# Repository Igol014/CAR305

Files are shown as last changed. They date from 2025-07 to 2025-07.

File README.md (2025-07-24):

# Инструкция по сборке и запуску автономной модели автомобиля RC305

## Вам понадобится следующий набор инструментов
  - Паяльник (думаю понятно для чего 🤔)
  - Шуруповерт (для рассверливания крепежных отверстий и сверления новых 👍)
  - Клеевой пистолет (для укладки проводов в корпусе, фиксации разъема аккумулятора, да и просто на случай, если увлеклись сверлением 🙊)
  - Отвертки (скорее всего PH1 и PH2, но зависит от использованных винтиков 🤷‍♂️)
  - Шестигранники (если не хватит обычных винтиков 😎)
## Использованные компоненты
  - Колесо диаметром 88 мм 4 шт;
  - Мини-компьютер Raspberry Pi 5 8 GB Cortex-A76;
  - Понижающий DC-DC 5A XL4005 2 шт;
  - Мотор-редуктор с энкодерами 2 шт;
  - Драйвер L298N;
  - Тумблер-выключатель;
  - Arduino Nano V3.0 USB-C ATMEGA328P FT232(Old Bootloader);
  - Набор проводов для пайки;
  - Аккумулятор LiPo 4S 3300 mAh 40C(NXE) 14.8В;
  - Лазерный дальномер(LiDAR) для робота-пылесоса Xiaomi Mijia Mi Robot Vacuum Cleaner 1S;
  - Модуль IMU 9-DOF GY-85;
  - Сервопривод TianKongRC TD-8120MG;
  - Пины мама-мама 20 шт.
## Корпус

Модель корпуса нашей машинки выглядит следующим образом

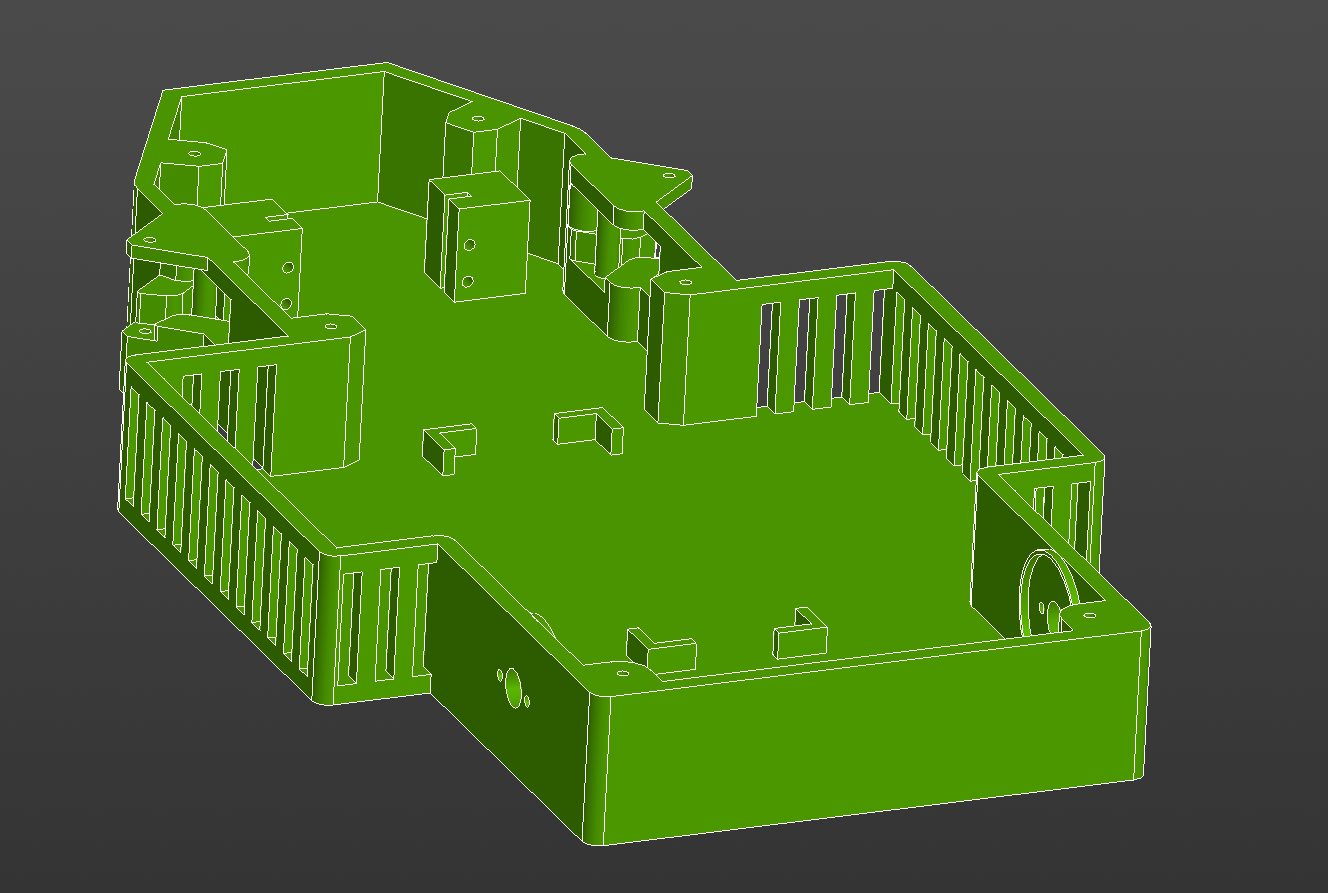
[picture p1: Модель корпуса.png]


Если нет собственных "производственных мощностей", всегда можно воспользоваться услугами __[студий 3D печати](https://uslugi.yandex.ru/213-moscow/category/raznoe/poligraficheskie-uslugi/3dpechat--5635)__

В случае выбора лёгкого пути, смело можно пропускать данный раздел

Для печати корпуса необходим 3D принтер с рабочим полем **400x300 мм**

Выбор материала

Краткая информация об основных видах пластика

| **Параметр** | **ABS** | **PLA** | **PETG** |
|---|---|---|---|
| **Печать** | Капризен, требует закрытого бокса и вентиляции | Очень прост, идеален для новичков | Умеренно прост, требует настройки |
| **Прочность** | Прочный, ударостойкий | Жесткий, но хрупкий при ударе и холоде | Прочный, гибкий, устойчив к излому |
| **Темп. стойкость** | Высокая (-40…+80 °C) | Низкая (~50 °C, "плывёт" на солнце) | Средняя (~80 °C), подходит для большинства задач  |
| **Нетоксичность** | ❌ (выделяет вредные пары) | ✅ (безопасен, с запахом жареной еды) | ✅ (не пахнет, безопасен) |

Для нашего автомобиля будем использовать **PETG**

Для печати корпуса воспользуемся специальной программой __[OrcaSlicer](https://orcaslicer.com/)__

Выставим основные параметры печати следующими:

- Температура экструзии — 215-245°C;

- Температура стола — 20-80°C;

- Процент заполнения — 60%;

## Устанока навесных компонентов
Во время установки ориентируйтесь на компоновку деталей с фотографии ниже.

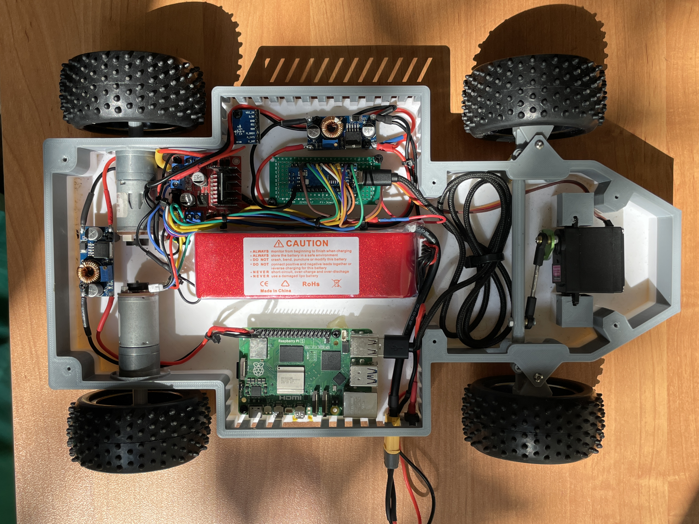
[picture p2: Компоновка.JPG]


1) Начнём с установки двигателей и задних колёс;
    - Закрепите задние моторы на корпус винтами M3;
    - Установите втулки на валы моторов и зафиксируйте их сбоку винтом чрез специальное отверствие во втулке винтом M3;
    - Установите колесо на втулку, зафиксируйте колесо на валу винтом M4.
2) Монтаж передних колес и рулевого управления;
    - Установите поворотные кулаки на винты M3;
    - Установите сервопривод, закрепите его винтами M2.5;
    - Соедините тягу сервопривода к переходной пластине сервопривода;
    - Соедините поворотные кулаки рулевой рейкой с помощью винтов M3;
    - Соедините рулевую рейку с тягой сервопривода.
    - Установите гайку-проставку на колесо и вставьте в поворотный кулак. Закрепите колеса винтами M4, затянув с небольшим усилием с внутренней стороны колеса самоконтрящуюся гайку.
3) Далее монтируем стойки для установки __Raspberry Pi 5__, __лидара__, __2-ух DC-DC преобразователей__, __IMU__ и __Arduino Nano__. Стойки для лидара устанавливаем на крышку корпуса, делаем отверстие в крышке для вывода проводов. Устанавливать лидар можно в произвольном месте(__Для всех компонентов, помимо лидара, используйте низкие стойки, примерно 0.5 см высотой__);
4) Монтируем драйвер моторов, DC-DC преобразователи, IMU, сервопривод рулевого управления;
5) Устанавливаем кнопку питания в корпус, прокладываем провод питания с разъемом XT60 в корпусе;
6) Настраиваем преобразователи на **5В** путем вращения винта против часовой стрелки;
7) Монтируем Arduino;
8) Монтируем проводку по схеме(за исключением Raspberry Pi);

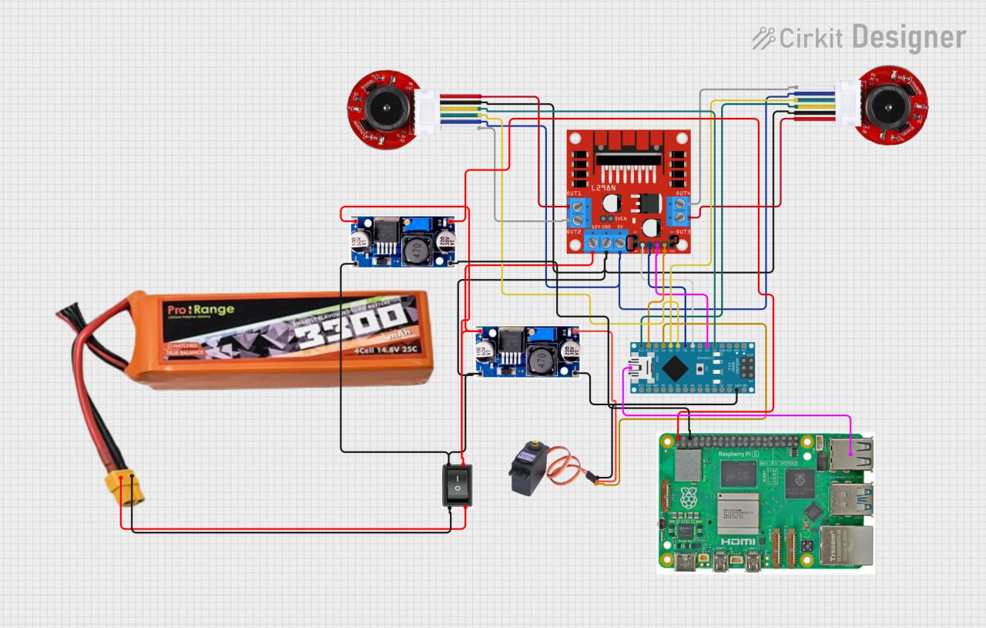
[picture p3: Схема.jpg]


9) Устанавливаем Raspberry Pi и подключаем ее согласно схеме;
10) Загружаем скетч на Arduino(__Обязательно к прочтению пункт с возможными проблемами перед работой с Arduino__);
11) Подключаем Arduino к Raspberry Pi через провод USB-C (__нужно использовать мягкий, гибкий провод, другой не подойдет__);
12) Крепим крышку(можно на винты, можно на саморезы)
13) Устанавливаете ОС Ubuntu на Raspberry Pi;
14) Подготовка Raspberry Pi к работе
      
    Для удаленного управления машинкой через Raspberry Pi был использован протокол SSH, с помощью которого можно получить доступ к терминалу и отправлять команды на малинку. Перед подключением по этому протоколу, нужно         сначала установить необходимые пакеты на Raspberry и провести некоторые манипуляции. Перед всеми махинациями нужно обновить системные пакеты во избежание различного рода ошибок во время установки. Сделать это можно следующей командой:

      ```
      sudo apt update
      ```
    - Установка SSH-сервера;
       
       Для установки SSH-сервера используем команду:
       ```
       sudo apt install openssh-server
       ```
    - Проверка статуса службы;
       
       Проводим проверку и убеждаемся в том, что установка прошла правильно и все работает штатно:
       ```
       sudo systemctl status ssh
       ```
    - Настройка фаервола(Если не планируете использовать - можно пропустить);
       
       Если вы хотите использовать фаервол, то в его настройках нужно разрешить подключеие к системе по протоколу SSH:
       ```
       sudo ufw allow ssh
       ```
       Если вы установили свой порт для подключения к серверу по протоколу SSH, то выполните следующую команду:(по умолчанию стоит порт 22, менять его не рекомендую):
       ```
       sudo ufw allow 'ваш порт'
       ```
       После выполнения вышеперечисленных команд, включаем фаервол:
       ```
       sudo ufw enable
       ```
    - Определить IP-адрес для подключения;
       
       Для определения IP-адреса нужно выполнить следующую команду:
       ```
       ip address
       ```
       После выполнения данной команды в терминале появится информация о различных сетевых интерфейсах. Нам нужно найти строку wlan и ниже нее будет нужная нам информация. Ищем строку, похожую на эту:
       ```
       inet 198.168.1.100/24
       ```
       В данном случае, IP-адрес - 198.168.1.100.
    - Подключение к Raspberry Pi по протоколу SSH через внешнее устройство;
       
       Для работы с SSH я рекомендую использовать программу [Termius](https://www.termius.com/). Она бесплатная, с приятным и понятным интерфейсом и большим количеством предоставляемых ползователю возможностей. Скачать ее можно в магазине приложений Microsft Store.
       После установки приложения ищем в интерфейсе кнопку NEW HOST. Справа появляется выпадающее меню. В колонке Address вводим IP-адрес, ранее нами полученный. После ищем колонку с названием 'SSH on 22 port'(22 меняем на свой порт, если во время установки порт по умолчанию был вами изменен). В этой колонке будут поля 'Username' и 'Password'. В них нужно ввести имя пользователя и пароль, которые вы задали во время установки Ubuntu на Raspberry Pi. Все, поздравляю, на этом настройка подключения закончена, ищем в этом выпадающем меню зеленую кнопку 'Connect' и можно работать удаленно с малинкой. Termius также поддерживает удаленную передачу файлов через SFTP, поэтому малинку можно смело ставить в корпус машинки и больше ее не трогать, все необходимые операции легко можно провести удаленно, без физического подключения к Raspberry Pi.
    - __Финал!__ Загружаем код на малинку и запускаем его.
   
       Termius, как я ранее уже писал, поддерживает работу с файлами. Для того, чтобы перенести наш [код](https://github.com/Igol014/RC305/blob/main/Код/rasp.py) на малинку, в приложении ищем сверху вкладку SFTP и подключаемся к Raspberry Pi. Предыдущее подключение должно сохраниться, поэтому тут ничего сложного, вам нужно нажать только одну кнопку.
       После подключения перед вами будет два поля: слева и справа. Слева - директории вашего компьютера, справа - директории малинки. Переносите его в удобную вам директорию.
        Далее, на Raspberry Pi нужно установить ПО для работы с Python:
       ```
       sudo apt install python3
       ```
       ```
       sudo python3 -m venv <RC305>
       ```
       ```
       source <RC305>/bin/activate
       ```
       ```
       pip install pyserial
       ```
       Для запуска нашей программы, переходим в директорию, в которую ранее разместили rasp.py с помощью команды:
       ```
       cd 'путь до нужной директории'
       ```
       После, вводим следующую команду:
       ```
       sudo python3 rasp.py
       ```
      
### Готово!



## Возможные проблемы

- Не увлекайтесь рассверливанием отверстий при установке рулевого управления и стоек для компонентов! В первом случае будет большой люфт рулевого управления, вследствие чего автомобиль не сможет ровно держать курс, а во втором случае стойки не будут надежно зафиксированы в корпусе, что в будущем приведем к произвольному демонтажу компонентов при эксплуатации.
- Холодная пайка - ваш враг. Хорошенько прогревайте контакты во время пайки, так как это исключит неприятные моменты, связанные с отошедшей пайкой или плохим контактом.
- Надежно фиксируйте провода в зажимах, в противном случае будет плохой контакт или вовсе его отсутствие.
- При работе с Arduino не подключайте ее напрямую к компьютеру, используйте USB-hub с внешним питанием. Не думаю, что вы будете использовать оригинальную Arduino, а китайские иногда сходят с ума, умирают сами и забирают за собой технику, подключенную к ней.
- Raspberry Pi подключаете к Arduino в самую последнюю очередь, когда проверили все контакты и соединения и убедились, что все работает в штатном режиме. Спалить малинку - очень неприятно.

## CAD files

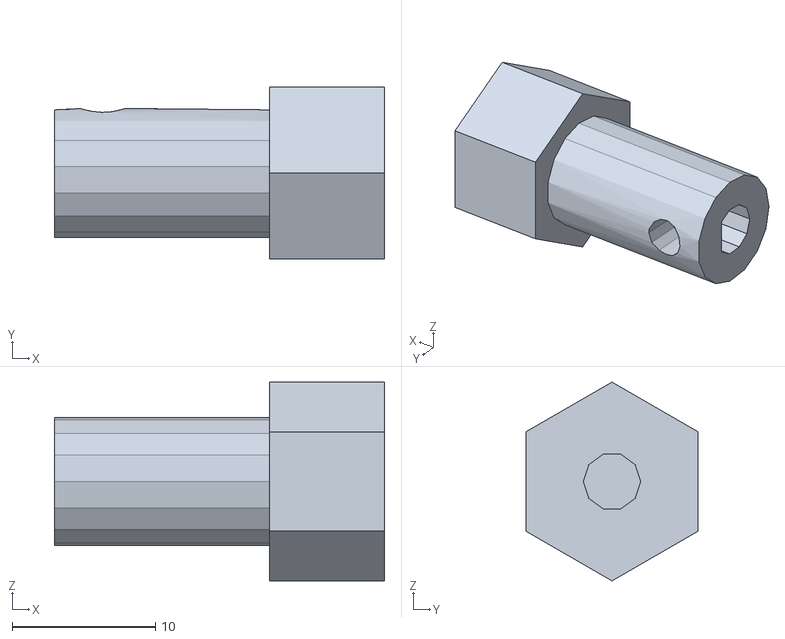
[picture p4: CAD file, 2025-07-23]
Модель/Втулка заднего колеса.stl
23.0 x 12.0 x 13.9

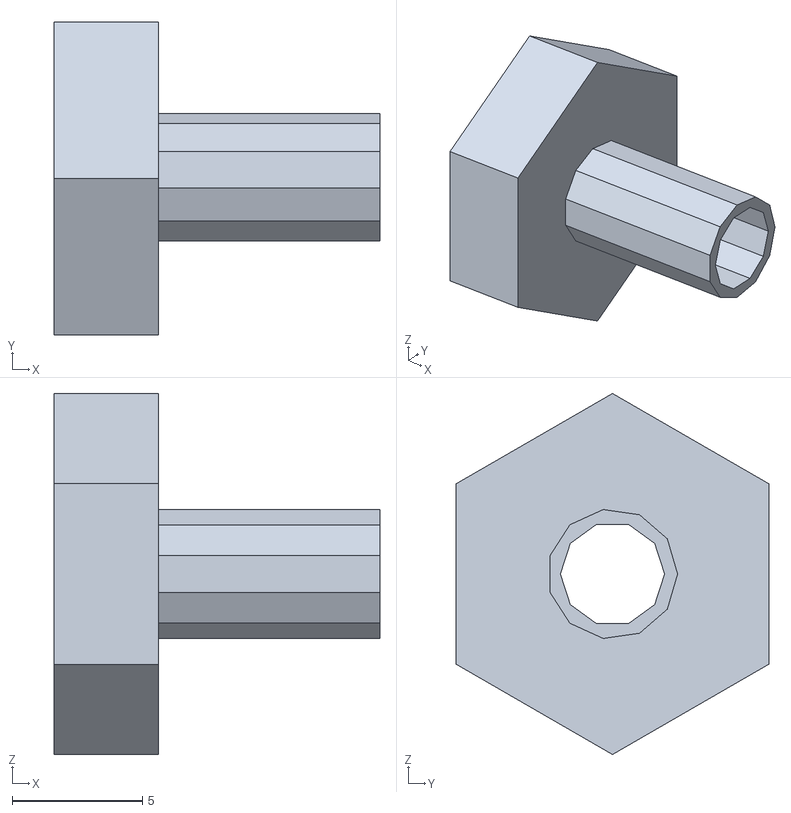
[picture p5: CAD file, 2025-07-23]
Модель/Гайка-проставка для колеса.stl
12.5 x 12.0 x 13.9

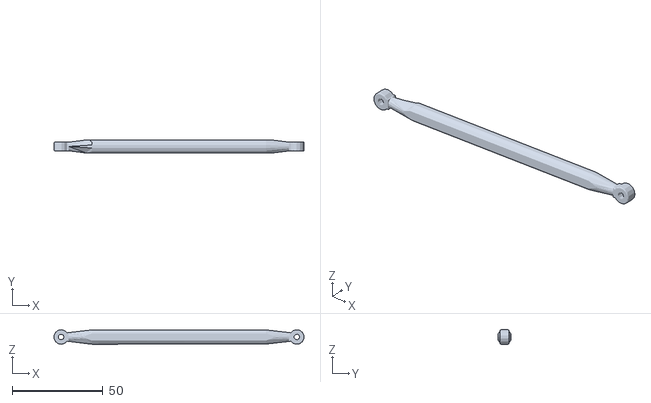
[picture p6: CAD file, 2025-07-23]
Модель/Рулевая тяга.stl
137.4 x 7.05 x 8.00

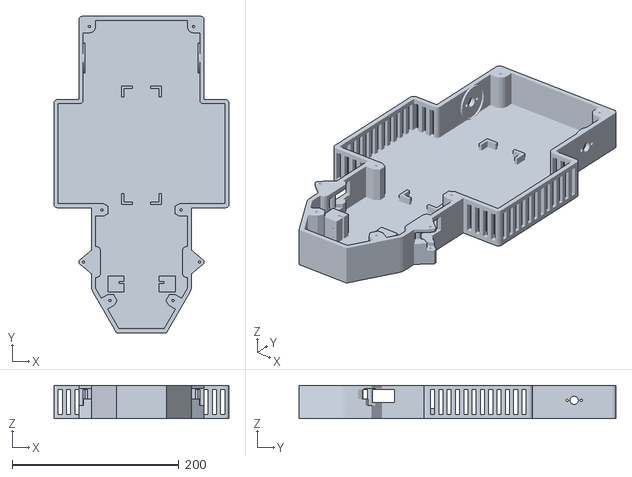
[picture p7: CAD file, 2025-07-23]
Модель/Рама.stl
210.0 x 380.0 x 40.0

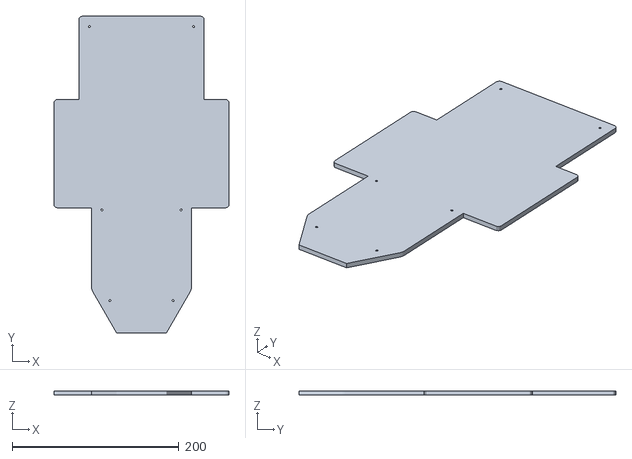
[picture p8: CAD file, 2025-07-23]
Модель/Крышка корпуса.stl
210.0 x 380.0 x 5.00

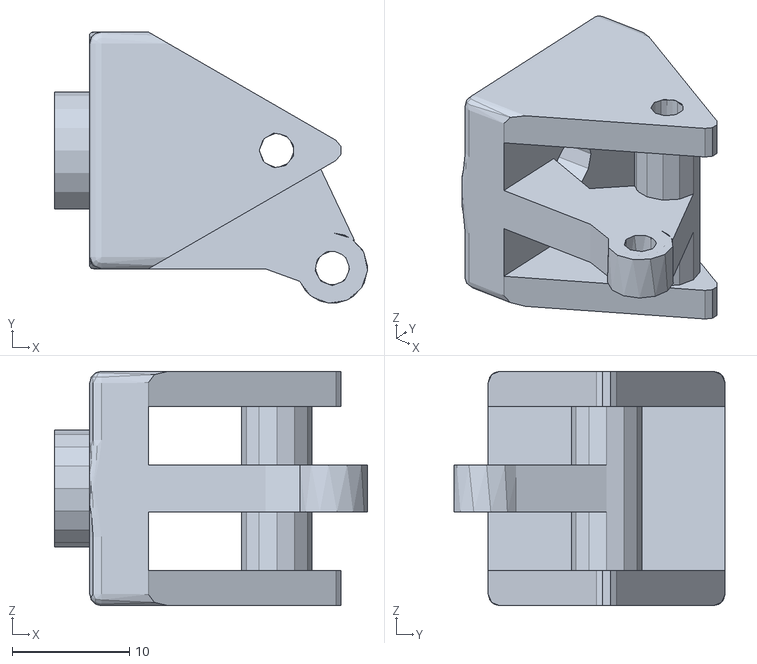
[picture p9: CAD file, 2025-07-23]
Модель/Поворотный кулак.stl
26.7 x 23.1 x 20.0

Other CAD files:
Модель/Крепление Лидара 40мм высота.stl

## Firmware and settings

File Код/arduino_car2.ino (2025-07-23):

#include <Servo.h>

// Конфигурация пинов для драйвера L298N
#define IN1 5  // Левый мотор (вперёд)
#define IN2 6   // Левый мотор (назад)
#define IN3 3   // Правый мотор (вперёд)
#define IN4 11   // Правый мотор (назад)

// Конфигурация сервопривода
#define SERVO_PIN 9
Servo myServo;
int servoAngle = 90;  // Текущий угол сервопривода (0-180)

// Конфигурация энкодеров
#define ENCODER_LEFT_A 2   // Канал A левого энкодера (INT0)
#define ENCODER_LEFT_B 7   // Канал B левого энкодера
#define ENCODER_RIGHT_A 12  // Канал A правого энкодера (INT1)
#define ENCODER_RIGHT_B 8  // Канал B правого энкодера

// Переменные состояния
int motorSpeed = 0;      // Общая скорость (-255 до 255)
int leftSpeed = 0;       // Скорость левого мотора
int rightSpeed = 0;      // Скорость правого мотора
volatile long leftEncoderCount = 0;   // Счетчик левого энкодера
volatile long rightEncoderCount = 0;  // Счетчик правого энкодера
unsigned long lastEncoderPrint = 0;   // Время последнего вывода энкодеров

void setup() {
  // Инициализация моторов
  pinMode(IN1, OUTPUT);
  pinMode(IN2, OUTPUT);
  pinMode(IN3, OUTPUT);
  pinMode(IN4, OUTPUT);
  stopMotors();
  
  // Инициализация сервопривода
  myServo.attach(SERVO_PIN);
  myServo.write(servoAngle);
  
  // Инициализация энкодеров
  pinMode(ENCODER_LEFT_A, INPUT_PULLUP);
  pinMode(ENCODER_LEFT_B, INPUT_PULLUP);
  pinMode(ENCODER_RIGHT_A, INPUT_PULLUP);
  pinMode(ENCODER_RIGHT_B, INPUT_PULLUP);
  
  // Настройка прерываний для энкодеров
  attachInterrupt(digitalPinToInterrupt(ENCODER_LEFT_A), updateLeftEncoder, CHANGE);
  attachInterrupt(digitalPinToInterrupt(ENCODER_RIGHT_A), updateRightEncoder, CHANGE);
  
  // Инициализация последовательного порта
  Serial.begin(115200);
  Serial.println("System Ready");
}

void loop() {
  // Обработка команд с последовательного порта
  if (Serial.available()) {
    handleCommand(Serial.read());
  }
  
  // Периодическая отправка данных о состоянии
  if (millis() - lastEncoderPrint > 100) {
    Serial.print("SERVO:");
    Serial.print(servoAngle);
    Serial.print("|MOTORS:");
    Serial.print(leftSpeed);
    Serial.print(",");
    Serial.print(rightSpeed);
    Serial.print("|ENCODERS:");
    Serial.print(leftEncoderCount);
    Serial.print(",");
    Serial.println(rightEncoderCount);
    
    lastEncoderPrint = millis();
  }
  
  // Управление моторами на основе значений энкодеров
  controlMotors();
}

void handleCommand(char cmd) {
  switch(cmd) {
    case 'W': motorSpeed = min(255, motorSpeed + 25); break;   // Вперед
    case 'S': motorSpeed = max(-255, motorSpeed - 25); break;  // Назад
    case 'X': motorSpeed = 0; break;                          // Стоп
    case 'A': servoAngle = max(0, servoAngle - 10); break;     // Серво влево
    case 'D': servoAngle = min(180, servoAngle + 10); break;   // Серво вправо
  }

  // Обновляем сервопривод
  myServo.write(servoAngle);
  
  // Устанавливаем скорости для моторов
  leftSpeed = -motorSpeed;  // Инверсия для левого мотора
  rightSpeed = motorSpeed;  // Правый мотор без изменений
  
  setMotors(leftSpeed, rightSpeed);
  Serial.print("MOTORS:");
  Serial.print(leftSpeed);
  Serial.print(",");
  Serial.println(rightSpeed);
}

void setMotors(int left, int right) {
  // Левый мотор (инвертированный)
  if(left > 0) {
    analogWrite(IN1, left);  // Вперед
    analogWrite(IN2, 0);
  } else if(left < 0) {
    analogWrite(IN1, 0);
    analogWrite(IN2, abs(left)); // Назад
  } else {
    analogWrite(IN1, 0);
    analogWrite(IN2, 0); // Стоп
  }
  
  // Правый мотор (обычное управление)
  if(right > 0) {
    analogWrite(IN3, right); // Вперед
    analogWrite(IN4, 0);
  } else if(right < 0) {
    analogWrite(IN3, 0);
    analogWrite(IN4, abs(right)); // Назад
  } else {
    analogWrite(IN3, 0);
    analogWrite(IN4, 0); // Стоп
  }
}

void stopMotors() {
  analogWrite(IN1, 0);
  analogWrite(IN2, 0);
  analogWrite(IN3, 0);
  analogWrite(IN4, 0);
}

// Обработчики прерываний для энкодеров
void updateLeftEncoder() {
  if (digitalRead(ENCODER_LEFT_A) == digitalRead(ENCODER_LEFT_B)) {
    leftEncoderCount++;
  } else {
    leftEncoderCount--;
  }
}

void updateRightEncoder() {
  if (digitalRead(ENCODER_RIGHT_A) == digitalRead(ENCODER_RIGHT_B)) {
    rightEncoderCount++;
  } else {
    rightEncoderCount--;
  }
}

// Функция управления моторами на основе значений энкодеров
void controlMotors() {
  // Здесь можно добавить логику для управления моторами на основе значений энкодеров
  // Например, можно использовать PID-контроллер для поддержания заданной скорости
  // или корректировки направления движения на основе разницы между значениями энкодеров.
  
  long leftError = leftEncoderCount;  // Получаем текущее значение левого энкодера
  long rightError = rightEncoderCount; // Получаем текущее значение правого энкодера
  

  
  // Убедитесь, что скорости не выходят за пределы
  leftSpeed = constrain(leftSpeed, -255, 255);
  rightSpeed = constrain(rightSpeed, -255, 255);
  
  // Устанавливаем новые скорости моторов
  setMotors(leftSpeed, rightSpeed);
}

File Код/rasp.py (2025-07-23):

import serial
import sys
import tty
import termios

# Настройка UART (замените порт при необходимости)
ser = serial.Serial('/dev/ttyUSB0', 115200, timeout=1)

def send_command(cmd):
    ser.write(cmd.encode())
    print(f"Отправлено: {cmd}")

def get_key():
    # Настройка терминала для чтения клавиш без Enter
    fd = sys.stdin.fileno()
    old_settings = termios.tcgetattr(fd)
    try:
        tty.setraw(sys.stdin.fileno())
        key = sys.stdin.read(1)
    finally:
        termios.tcsetattr(fd, termios.TCSADRAIN, old_settings)
    return key

if __name__ == "__main__":
    print("Управление: W/A/S/D/X/C. Выход: Q")
    try:
        while True:
            key = get_key().upper()
            if key in ['W', 'A', 'S', 'D', 'X', 'C']:
                send_command(key)
            elif key == 'Q':
                print("Выход...")
                break

    except KeyboardInterrupt:
        print("\nПрограмма завершена.")
    finally:
        ser.close()
